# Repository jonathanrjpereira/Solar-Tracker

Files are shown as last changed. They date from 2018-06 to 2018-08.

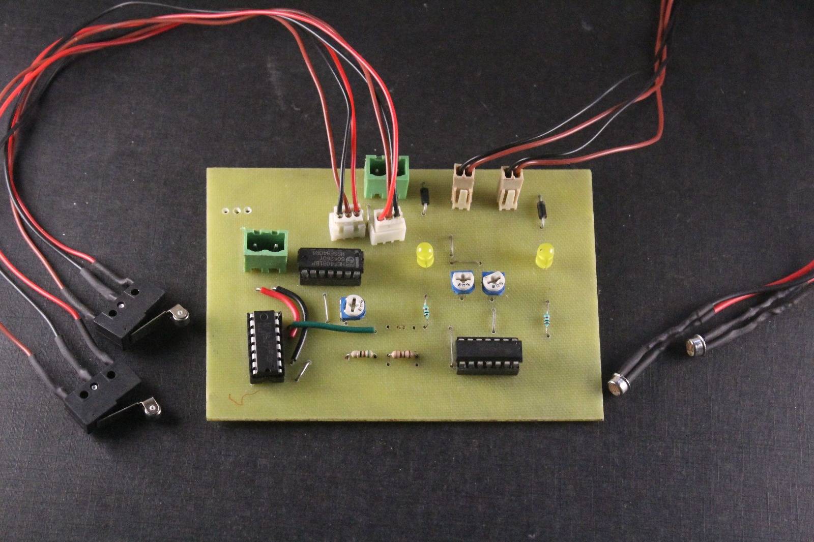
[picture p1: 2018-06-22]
Images/PCB.jpg

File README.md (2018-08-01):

# Solar-Tracker
Single Axis Solar Tracker without Microcontroller

|Parts|Specification|Quantity|
|--|--|--|
|L293D|Quadruple Half-H Drivers|1|
|LM324|Low-Power, Quad-Operational Amplifiers|1|
|HEF4081B|Quad 2-input AND gate|1|
|7805|5V Linear Regulator|1|
|Limit Switch|SPDT|2|
|LDR|Size & resistance varies according to your requirement|2|
|Potentiometers|5K Ohm|3|
|Resistors|1K Ohm|2|
|Diode|IN4001|2|
|LED|2V|2|
|DC Motor|9V or 12V|1|
|Power Supply|9V or 12V|1|
|Solar Panel|Optional|1|

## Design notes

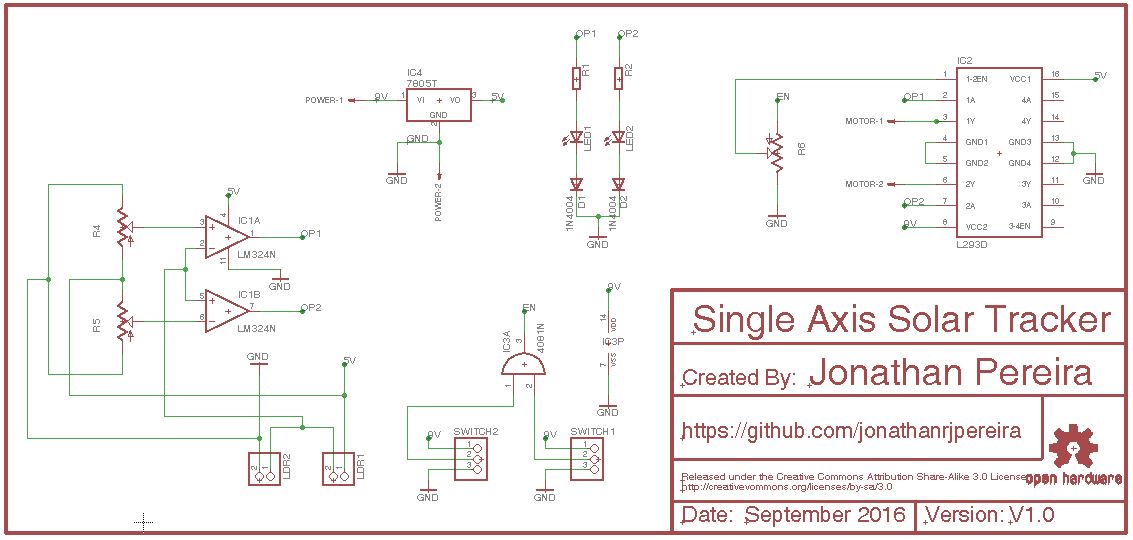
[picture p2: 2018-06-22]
Images/Schematic.JPG

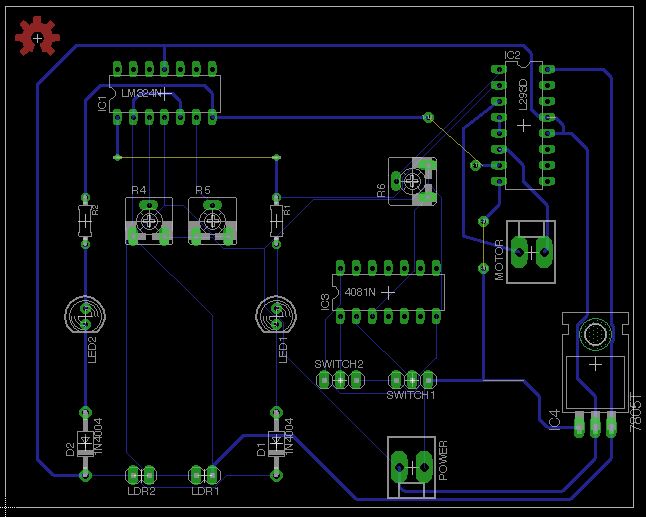
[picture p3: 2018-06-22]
Images/Board.JPG

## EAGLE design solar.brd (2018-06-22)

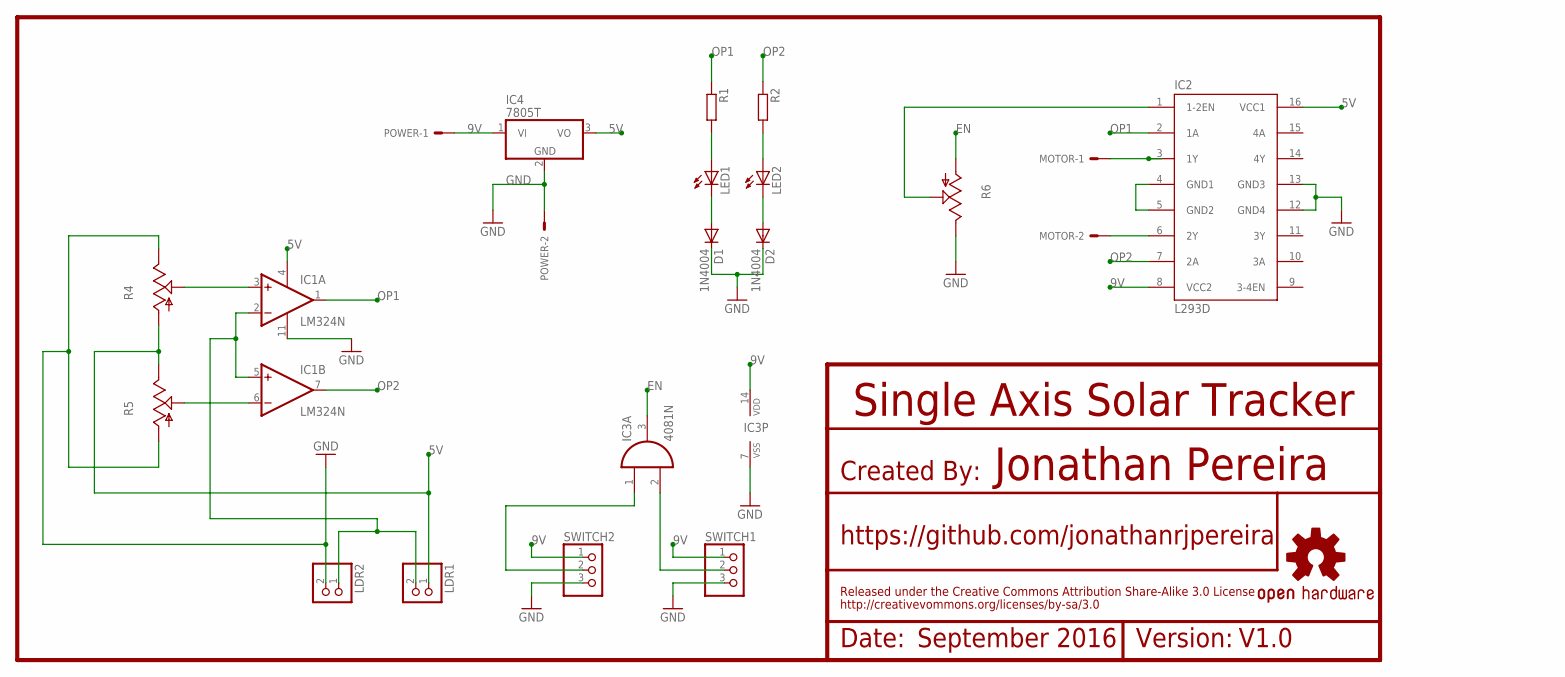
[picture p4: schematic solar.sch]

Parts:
D1, D2: 1N4004; DO41-10
IC1: LM324N; DIL14
IC2: L293D; DIL16
IC3: 4081N; DIL14
IC4: 7805T; TO220H
LDR1, LDR2: PINHD-1X2; 1X02
LED1, LED2: LED5MM
LOGO1: OSHW-LOGOL-COPPER; OSHW-LOGO-L_COPPER
MOTOR: KK-156-2
POWER: KK-156-2
R1, R2: R-EU_0204/7; 0204/7
R4, R5, R6: TRIM_US-CA6V; CA6V
SWITCH1, SWITCH2: PINHD-1X3; 1X03

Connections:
5V: IC1.4 (V+), IC2.16 (VCC1), IC4.3 (VO), LDR1.1, R4.A, R5.E
9V: IC2.8 (VCC2), IC3.14 (VDD), IC4.1 (VI), POWER.1, SWITCH1.1, SWITCH2.1
EN: IC3.3 (O), R6.A
GND: D1.C, D2.C, IC1.11 (V-), IC2.12 (GND4), IC2.13 (GND3), IC3.7 (VSS), IC4.2 (GND), LDR2.2, POWER.2, R4.E, R5.A, R6.E, SWITCH1.3, SWITCH2.3
unnamed: IC2.3 (1Y), MOTOR.1
unnamed: IC2.6 (2Y), MOTOR.2
unnamed: IC2.4 (GND1), IC2.5 (GND2)
unnamed: IC2.1 (1-2EN), R6.S
unnamed: IC3.1 (I0), SWITCH2.2
unnamed: IC3.2 (I1), SWITCH1.2
unnamed: IC1.2 (-IN), IC1.5 (+IN), LDR1.2, LDR2.1
unnamed: IC1.3 (+IN), R4.S
unnamed: IC1.6 (-IN), R5.S
unnamed: LED1.A, R1.2
unnamed: LED2.A, R2.2
unnamed: D2.A, LED2.K (C)
unnamed: D1.A, LED1.K (C)
OP1: IC1.1 (OUT), IC2.2 (1A), R1.1
OP2: IC1.7 (OUT), IC2.7 (2A), R2.1

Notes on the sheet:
Date:
Version:
September 2016
V1.0
Single Axis Solar Tracker
Jonathan Pereira
Created By:
https://github.com/jonathanrjpereira
Released under the Creative Commons Attribution Share-Alike 3.0 License
http://creativevommons.org/licenses/by-sa/3.0

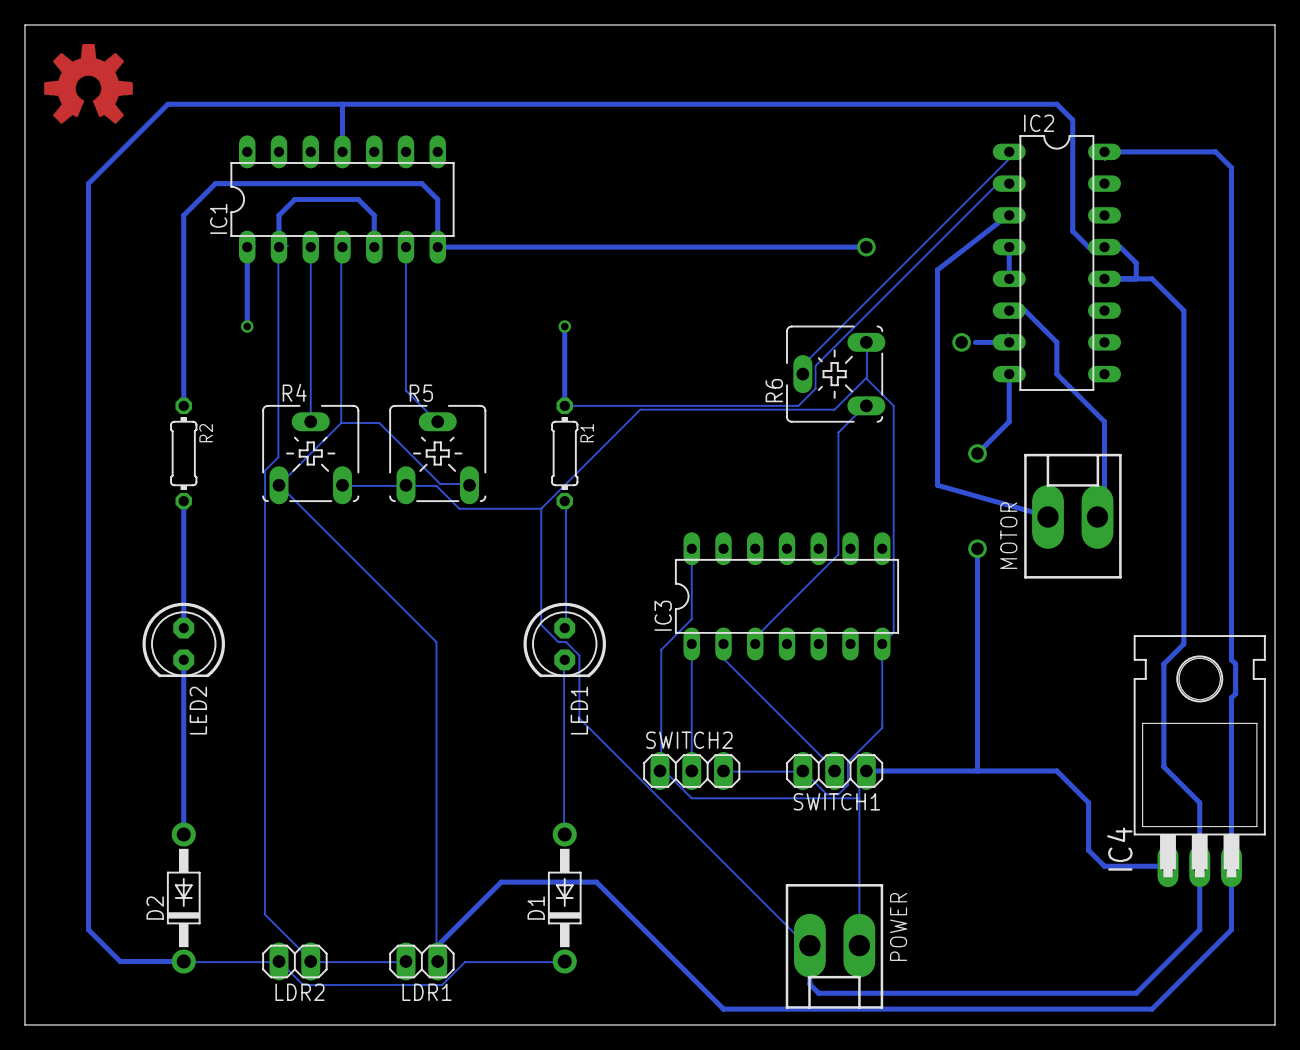
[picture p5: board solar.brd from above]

Board: 2 copper layers, 100.0 x 80.0 mm, 20 parts (0 on the bottom side), 19 nets.

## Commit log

2018-06-22 Eagle Schematic
    [solar.sch]
2018-06-22 Eagle Board
    [solar.brd]
2018-06-22 Schematic & Board Pictures

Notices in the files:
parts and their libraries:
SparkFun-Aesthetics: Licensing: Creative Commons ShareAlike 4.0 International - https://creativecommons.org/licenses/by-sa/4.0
